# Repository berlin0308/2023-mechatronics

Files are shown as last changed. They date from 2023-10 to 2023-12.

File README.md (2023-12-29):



# I. Introduction

Our robot is designed to be controlled remotely through video streaming. Its primary functions include navigating around and performing vacuuming tasks. Our core philosophy is to minimize space to enhance the robot's agility. In addition, careful study and design of the vacuum is essential to ensure sufficient cleaning efficiency. 
However, fulfilling both requirements simultaneously is not an easy task. In the next chapter, we divided our system design into three main parts: Mechanical Design, Hardware & Electrical Design, and Software & User Interface. 

# II. System Design

## 1.	Mechanical Design

### 1.1 Overview

Our robot is comprised of three layers in a circular design, allowing it to rotate in place. Its diameter is restricted to just 18 centimeters for enhanced agility. The main structural components are in the middle (in x, y axis) and underneath (in z axis) to ensure balance. 

The top layer mainly consists of an Arduino and RPi, forming the core for computation and control. The middle layer houses the vacuum and motor structures, along with the power control circuit. The lowest layer aligns the omnidirectional wheels, drive wheels, and vacuum nozzle at the same height to ensure the vacuum remains close to the ground, maximizing suction efficiency.



For securing each mechanical component, we strictly use keyholes and screws instead of direct adhesion. Additionally, with an emphasis on superior industrial design, the body of the robot features a combination of wood tones and white. This choice underlines a lightweight, minimalist, and homely style. 

### 1.2 Vacuum Design

Unlike other groups using fan-induced duct flow to direct dust into a collection box, we utilized a fan close to the ground to create a pressure difference, sucking in dust. Then, using centrifugal force, it disperses the dust to settle onto the dustbin. 

We adopted this method for two reasons: First, integrating the nozzle and dustbin into a single mechanism reduces space occupation, aligning with our core philosophy. Second, a fan positioned close to the ground minimizes pressure loss.

During the midterm test, we adopted a circular design as shown in Figure (a). However, due to the nozzle being too close to the ground and the opening too narrow, precise alignment was necessary to vacuum up scraps of paper. In the final test version, shown in Figure (b), we precisely adjusted the mechanism's height and enlarged the opening. Additionally, we conceived and validated a fact: a rectangular opening effectively creates turbulence in corners, enhancing the vacuum's cleaning performance.

Figure (c) provides a closer look. The blue region indicates the spatial occupation of the fan. Acting like a pump, the fan generates an airflow (red arrows) that dives into the interior with turbulence induced (orange arrows). The fan then disperses the dust (blue arrows), letting it to settle into the dustbin (grey arrows).



### 1.3 Front Sensor and Robotic Eyes 

During the mid-term test, we employed a video-streaming strategy but encountered visibility issues when the robot was too close to walls. To address this, we installed an ultrasonic sensor at the front for corner detection. Upon detecting a corner, the device activates 'storm' mode, which involves spinning in place with the vacuum on.

In addition, to enhance its appearance and for fun aspects, we equipped the front side with an LCD display that shows different expressions during various states, as illustrated in Figures (a), (b), and (c).



## 2. Hardware & Electrical Design

Figure (a) illustrates our focus on achieving seamless integration of diverse components within a comprehensive circuit to augment both the functionality and power efficiency of the robot. The integrated components encompass a battery box, switch, vacuum motor, wheel motor, motor driver, RGB LED, ultrasonic sensor, camera, LCD, relay, power converter, Raspberry Pi, and Arduino Uno. 

A notable feature of our approach is the incorporation of a power converter in tandem with a relay, facilitating the robot to operate all devices using only a single battery box. This innovation eliminates the necessity for external power sources, setting our design apart from other teams' configurations that commonly rely on supplementary mobile power supplies.



## 3. Software & User Interface

Figure (b) represents the user interface developed by our team for this project. Unlike other groups utilizing App Inventor or other pre-existing toolkits, our team constructed the operational interface using HTML. Beyond the fundamental functionalities of basic directional controls for upward, downward, leftward, and rightward movement, our interface incorporates an additional feature known as the 'storm' function, depicted by the lightning cloud icon in Figure (b). This function enables powerful vacuuming upon reaching areas with accumulated dust.

Furthermore, the background design adopts a cyberpunk style to align with the visually striking appearance of our robotic vacuum cleaner. This cohesive design approach aims to ensure consistency between the device's aesthetics and its user interface.

The innovative use of HTML in crafting the interface sets our project apart, offering a tailored and visually engaging control system for the user. This deliberate design choice not only enhances usability but also complements the futuristic and captivating appeal of our robotic cleaner.

Figure (c) illustrates the conceptual diagram depicting the intercommunication and interaction between backend programs. Through interface buttons, messages are transmitted to 'main.py,' residing within our Raspberry Pi (RPI), which further relays these instructions via serial transmission to the Arduino for execution. This successful process fulfills the objectives of the class, specifically achieving communication and mechanical integration between the RPI and Arduino.
 
All these programs are hosted within our RPI, allowing us to utilize SSH from a computer within the same network domain for remote control. Employing these methods and technologies reflects our aim to simulate real-world operational environments for robotic vacuum cleaners. Typically, these operations involve remote communication via the internet from home environments. Therefore, this concept aligns with the core principle driving the initial design of our software.

# III. Discussion

## 1.	 Challenges

### 1.1	Mechanical Design



### 1.2	Software System Control



## 2.	Test Reviews



# IV.	Appendix

## Members and Teamwork



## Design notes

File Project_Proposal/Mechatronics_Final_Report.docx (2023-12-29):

2023 Fall

Mechatronics and System Design-Mechatronics IV

Final Project Report

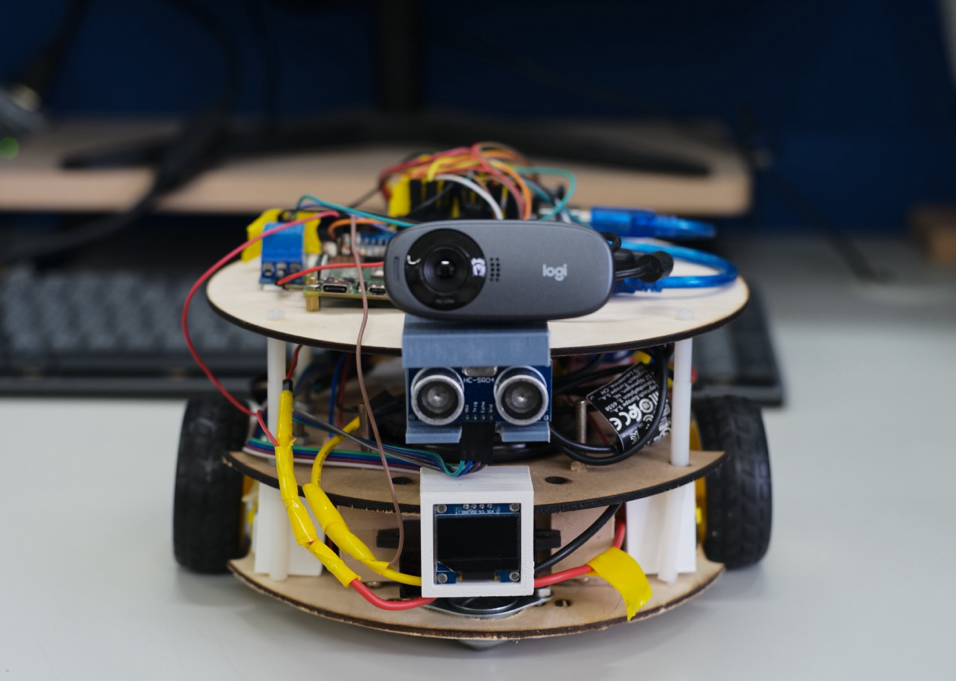
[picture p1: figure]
一張含有 室內, 玩具汽車, 比例模型, 玩具 的圖片 自動產生的描述

Group VI

Members:

B09611007 陳柏霖 (Po-Lin Chen)

B09611010 鄧世群 (Shih-Chun Deng)

B09611043 陳冠霖 (Guan-Lin Chen)

B08204024 陳冠宇 (Kuan-Yu Chen)

Abstract

This project report outlines the design and development of our compact, agile vacuum robot, engineered for remote operation via video streaming. The report delves into three primary areas of system design: Mechanical Design, Hardware & Electrical Design, and Software & User Interface.

In the Mechanical Design section, the report emphasizes the robot’s three-layer circular structure that enables it to rotate in place and maintain balance, with a strictly limited diameter for improved agility. A novel vacuum design with a ground-level fan and centrifugal dust dispersal mechanism is highlighted, showcasing the team’s unique approach to minimizing space while maintaining cleaning efficiency. The design also incorporates ultrasonic sensors and robotic eyes represented by an LCD display for enhanced functionality and interactivity.

Hardware & Electrical Design details the integration of components within the robot’s circuitry to optimize functionality and power efficiency. A key innovation is the use of a single battery box to operate all devices, which effectively reduces excess weight, setting our design apart from other teams that rely on supplementary mobile power supplies.

Software & User Interface development is recognized for its custom HTML-based control interface, featuring a 'storm' function for intensified vacuum cleaning and a cyberpunk-style visual theme to match the robot's aesthetics.

The report also discusses challenges encountered in the system development, with solutions such as adjustments to the robot's height, wheel support, vacuum nozzle shape for the mechanical aspect, and buffering to address with transmitting delays for the software.

Strategic improvements from Mid-term to Final Testing phases, including enhanced practice, corner detection, and 'storm' mode, significantly reduced the time required to complete tasks.

Overall, this project showcases a successful integration of innovative design, component optimization, and user interface development to create a distinctive and efficient robotic vacuum cleaner.

Outline

I. Introduction ……………………………….……….…... 4
II. System Design ………………………………….…….… 4
1. Mechanical Design ………………………………..……….. 4
  1.1 Overview ………………………………………….…….. 4
  1.2 Vacuum Design ……………………………………..… 5
  1.3 Front Sensor and Robotic Eyes ………………… 6
2. Hardware & Electrical Design ………..……………..… 6
3. Software & User Interface …..………………………….. 7
III. Discussion ……………………………………….………. 9
1. Challenges ……………………………………………………… 9
2. Test Reviews …………………………………………..………. 9
IV. Reflections & Suggestions ……………..……….. 10
V. Appendix ………………………………….……………. 11
1. Members and Teamwork ……………………………… 11

I. Introduction

Our robot is designed to be controlled remotely through video streaming. Its primary functions include navigating around and performing vacuuming tasks. Our core philosophy is to minimize space to enhance the robot's agility. In addition, careful study and design of the vacuum is essential to ensure sufficient cleaning efficiency.

However, fulfilling both requirements simultaneously is not an easy task. In the next chapter, we divided our system design into three main parts: Mechanical Design, Hardware & Electrical Design, and Software & User Interface.

II. System Design

1. Mechanical Design

1.1 Overview

Our robot is comprised of three layers in a circular design, allowing it to rotate in place. Its diameter is restricted to just 18 centimeters for enhanced agility. The main structural components are in the middle (in x, y axis) and underneath (in z axis) to ensure balance.

The top layer mainly consists of an Arduino and RPi, forming the core for computation and control. The middle layer houses the vacuum and motor structures, along with the power control circuit. The lowest layer aligns the omnidirectional wheels, drive wheels, and vacuum nozzle at the same height to ensure the vacuum remains close to the ground, maximizing suction efficiency.

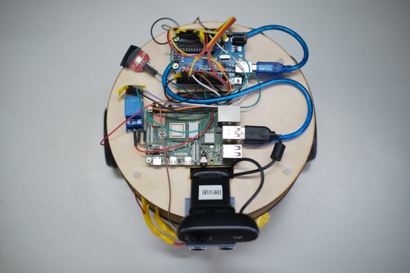
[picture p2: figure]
一張含有 電子工程, 電子產品, 電氣線路, 纜線 的圖片 自動產生的描述
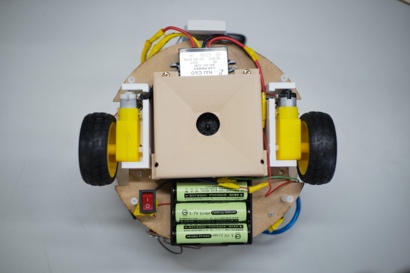
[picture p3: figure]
一張含有 玩具, 汽車零件, 輪胎, 輪 的圖片 自動產生的描述
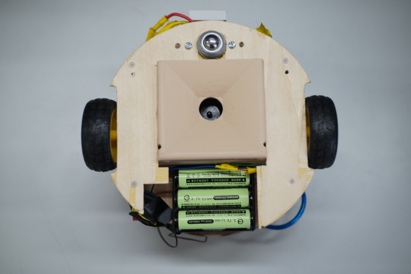
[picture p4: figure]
一張含有 玩具, 汽車零件, 車 的圖片 自動產生的描述

(a) Top layer | (b) Middle layer | (c) Bottom layer

For securing each mechanical component, we strictly use keyholes and screws instead of direct adhesion. Additionally, with an emphasis on superior industrial design, the body of the robot features a combination of wood tones and white. This choice underlines a lightweight, minimalist, and homely style.

1.2 Vacuum Design

Unlike other groups using fan-induced duct flow to direct dust into a collection box, we utilized a fan close to the ground to create a pressure difference, sucking in dust. Then, using centrifugal force, it disperses the dust to settle onto the dustbin.

We adopted this method for two reasons: First, integrating the nozzle and dustbin into a single mechanism reduces space occupation, aligning with our core philosophy. Second, a fan positioned close to the ground minimizes pressure loss.

During the midterm test, we adopted a circular design as shown in Figure (a). However, due to the nozzle being too close to the ground and the opening too narrow, precise alignment was necessary to vacuum up scraps of paper. In the final test version, shown in Figure (b), we precisely adjusted the mechanism's height and enlarged the opening. Additionally, we conceived and validated a fact: a rectangular opening effectively creates turbulence in corners, enhancing the vacuum's cleaning performance.

Figure (c) provides a closer look. The blue region indicates the spatial occupation of the fan. Acting like a pump, the fan generates an airflow (red arrows) that dives into the interior with turbulence induced (orange arrows). The fan then disperses the dust (blue arrows), letting it to settle into the dustbin (grey arrows).

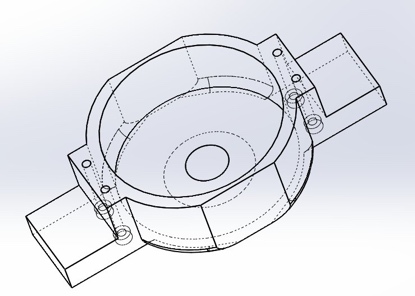
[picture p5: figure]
一張含有 寫生, 圖畫, 圓形, 圖表 的圖片 自動產生的描述
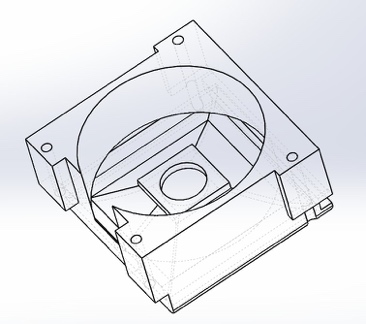
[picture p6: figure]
一張含有 寫生, 圖畫, 線條藝術, 圖表 的圖片 自動產生的描述
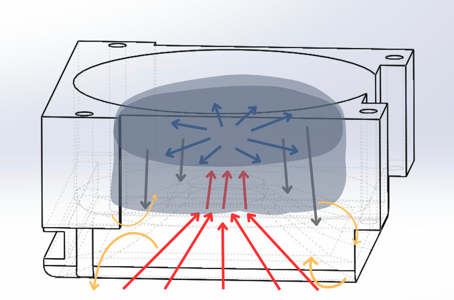
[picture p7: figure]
一張含有 行, 寫生, 設計, 藝術 的圖片 自動產生的描述

(a) Mid-term Version | (b) Final Version | (c) Fluid Velocity Field

1.3 Front Sensor and Robotic Eyes

During the mid-term test, we employed a video-streaming strategy but encountered visibility issues when the robot was too close to walls. To address this, we installed an ultrasonic sensor at the front for corner detection. Upon detecting a corner, the device activates 'storm' mode, which involves spinning in place with the vacuum on. (https://drive.google.com/file/d/1HJC3LFM9daGVQigIeRPdedcw-CsZ7EiV/view?usp=sharing)

In addition, to enhance its appearance and for fun aspects, we equipped the front side with an LCD display that shows different expressions during various states, as illustrated in Figures (a), (b), and (c).

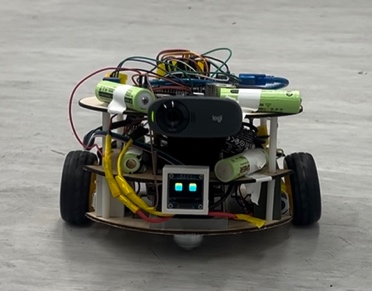
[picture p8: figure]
一張含有 輪, 輪胎, 動力運動, 汽車零件 的圖片 自動產生的描述
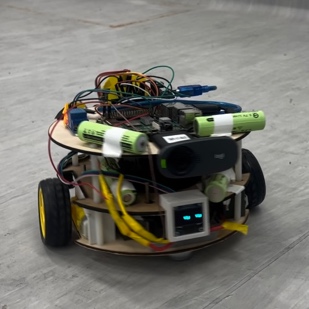
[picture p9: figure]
一張含有 輪, 輪胎, 車輛, 動力運動 的圖片 自動產生的描述
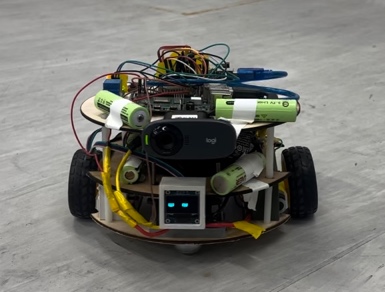
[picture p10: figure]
一張含有 輪, 輪胎, 汽車零件, 動力運動 的圖片 自動產生的描述

(a) Moving Forward | (b) Turning Left | (c) Turning Right

2. Hardware & Electrical Design

Figure (a) illustrates our focus on achieving seamless integration of diverse components within a comprehensive circuit to augment both the functionality and power efficiency of the robot. The integrated components encompass a battery box, switch, vacuum motor, wheel motor, motor driver, RGB LED, ultrasonic sensor, camera, LCD, relay, power converter, Raspberry Pi, and Arduino Uno.

A notable feature of our approach is the incorporation of a power converter in tandem with a relay, facilitating the robot to operate all devices using only a single battery box. This innovation eliminates the necessity for external power sources, setting our design apart from other teams' configurations that commonly rely on supplementary mobile power supplies.

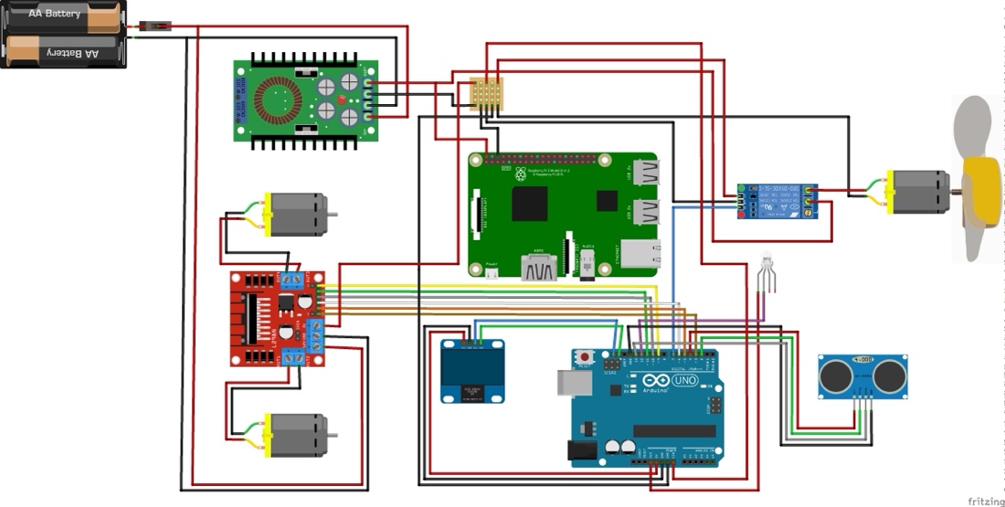
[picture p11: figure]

(a)

3. Software & User Interface

Figure (b) represents the user interface developed by our team for this project. Unlike other groups utilizing App Inventor or other pre-existing toolkits, our team constructed the operational interface using HTML. Beyond the fundamental functionalities of basic directional controls for upward, downward, leftward, and rightward movement, our interface incorporates an additional feature known as the 'storm' function, depicted by the lightning cloud icon in Figure (b). This function enables powerful vacuuming upon reaching areas with accumulated dust.

Furthermore, the background design adopts a cyberpunk style to align with the visually striking appearance of our robotic vacuum cleaner. This cohesive design approach aims to ensure consistency between the device's aesthetics and its user interface.

The innovative use of HTML in crafting the interface sets our project apart, offering a tailored and visually engaging control system for the user. This deliberate design choice not only enhances usability but also complements the futuristic and captivating appeal of our robotic cleaner.

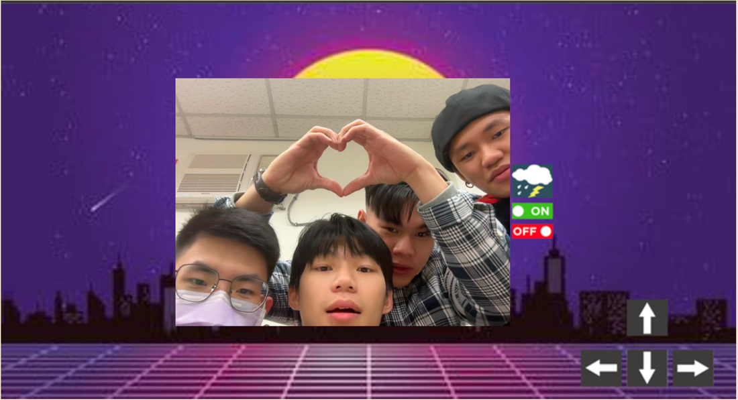
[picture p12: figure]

(b)

Figure (c) illustrates the conceptual diagram depicting the intercommunication and interaction between backend programs. Through interface buttons, messages are transmitted to 'main.py,' residing within our Raspberry Pi (RPI), which further relays these instructions via serial transmission to the Arduino for execution. This successful process fulfills the objectives of the class, specifically achieving communication and mechanical integration between the RPI and Arduino.

All these programs are hosted within our RPI, allowing us to utilize SSH from a computer within the same network domain for remote control. Employing these methods and technologies reflects our aim to simulate real-world operational environments for robotic vacuum cleaners. Typically, these operations involve remote communication via the internet from home environments. Therefore, this concept aligns with the core principle driving the initial design of our software.

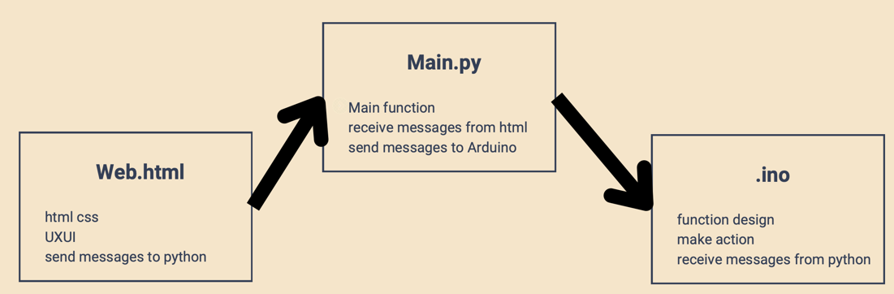
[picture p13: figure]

(c)

III. Discussion

1. Challenges
  1.1 Mechanical Design

Problems | Solutions
- Our vacuum was designed to be placed under the body of the vehicle, close to the ground. - The wheels often become splayed outward after running for a while, which caused our vehicle to get stuck during the journey. | - Adjusted vehicle’s height by adding a layer. - Made precise adjustments of the omni-wheel. - Redesigned the shape of the vacuum nozzle. - Designed and installed a bracket for motors.

  1.2 Software System Control

Problems | Solutions
- Delay when using UI buttons during the Mid-term Test, leading to multiple presses. - Excessive turning angles for left and right movements, making it difficult to accurately reach the targets. | - Introduced a buffer in the main program to alleviate the delay issue. - Adjusted control parameters for forward, backward, left, and right movements.

2. Test Reviews

Midterm Test | Final
- Insufficient testing before the mid-term. - Couldn't view the floor, preventing us from determining whether we had aligned with the target. - Wasted time wandering. | - Conducted more practice sessions for both manual and video-streaming control. - Introduced corner detection and ‘storm’ mode to efficiently complete the task. - Saved over half of the time during the final test.

VI. Reflections & Suggestions
1. B09611007陳柏霖 (Po-Lin Chen)

關於這堂課，我覺得專題有吸塵的元素蠻有趣的，也可以讓大家發揮創意。不過專題花費的時間其實超過想像，我主要負責的是機構設計，原以為期中之後車體定型就有時間協助軟體開發自走功能，沒想到期中之後車體要加裝一層、3D列印的支架和鎖孔都要更新、吸塵口機構迭代五次，其實也不夠時間做自走車了，剩下的時間只好拿來做角落偵測和機器人眼睛。認真算下來這學期花了68小時課外時間，以3學分的課而言有點多但還可接受。給課程的建議是可以更重視報告的呈現和工業設計，兩者都是系上其他課程未要求卻極為重要的素養，作為Capstone課程若能加強培養必能使同學畢業後更加體面且專業。

2. B09611010 鄧世群 (Shih-Chun Deng)

我負責電路設計與實踐的部分，包含線路焊接、硬體系統整合和改善。期中花費許多時間在與設計硬體的組員討論機構和線路的配合，因為我們想要盡可能將整組系統做得更加緊湊，節省空間和重量。組員都是四年級，大家每週的行程都相當不同，因此一開始明確的任務分配變得非常重要。使我們能夠根據任務內容配合出席的組員，更加有效率的完成任務。我認為這堂課的設計還需幾次的嘗試才能夠建立出完整的測試規則，避免太多變因造成不公平的可能。但還是非常感謝教授與助教的用心，大家都在這堂課學習到許多。

3. B09611043 陳冠霖 (Guan-Lin Chen)

我主要負責的部分是RPI主程式以及協助部分機構設計以及操作者，期中前我們把軟硬體的連線都大致完成，原本期待期末能以自走的方式呈現，結果期中發現吸塵有些狀況，加上對規則計分不夠熟悉，表現不佳。因此期末我們決定捲土重來，把機構重新修改，改善軟體以及熟練操作，期末有明顯進步。這學期的過程中很感謝組員的互相合作，加上不斷地修改調整以及溝通，讓我們從0開始到最後有一定的成果。也很感謝老師跟助教在這學期的協助，協助我們有一個能展現的舞台，作為大學4年最後一堂必修課，是一個很難忘的回憶。

4. B08204024 陳冠宇 (Kuan-Yu Chen)

在這個團隊中，我的主要責任是軟體架構，包括UX/UI設計和不同平台框架 間的溝通。大部分工作其實在期中評估之前就完成了，但由於期中成績不 盡理想，我們後來對程式進行了一些修改，以在專題結束時更加順暢地運 行。我認為這門課作為我們學業的最後一站，主題和內容都非常貼合。在 這個過程中需要的技能都是我們四年學習的累積，和這些同學一起完成最 後的專題任務感覺格外特別。看著大家從一開始的困惑到能夠高效地完成 分派的任務，這種轉變讓人深受觸動。唯一的遺憾是期中時間稍微不足 （雖然在期末有改善），以及某些規則可能使得比賽某些方面不太公平。 但無論如何，我非常感激大家的奉獻，也感謝我們的教授和助教所提供的 指導。

VII. Appendix
1. Members and Teamwork

| Po-Lin Chen | Shih-Chun Deng | Kuan-Yu Chen | Gaun-Lin Chen
Project Proposal | Mechanical Design, Materials, Proofreading, Refinement | System Diagram, Electrical Design | User Interface | Difficulties
~ Mid-term | components design, manufacturing, assembly | circuits, power, hardware testing | frontend, user interface | backend
Mid-term Trial & Test | testing | testing | testing, robot operator | testing
~ Final | components iterations, corner detect, robotic eyes | power circuits update | software fine-tuning | component design
Final Trial & Test | fine-tuning | fine-tuning | fine-tuning | fine-tuning, robot operator
Final Presentation | Mechanical Design, slides proofreading | Electrical Design, presenter | Software & UI, presenter | Discussion
Final Report | Abstract, Introduction, Mechanical Design, Proofreading, Refinement | Hardware & Electrical Design | Software & User Interface | Discussion

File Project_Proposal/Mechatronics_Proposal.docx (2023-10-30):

2023 Fall

Mechatronics and System Design-Mechatronics IV

Final Project Proposal

Group VI:

Members:

B09611007 陳柏霖 (Po-Lin Chen)

B09611010 鄧世群 (Shih-Chun Deng)

B09611043 陳冠霖 (Kaun-Lin Chen)

B08204024 陳冠宇 (Kuan-Yu Chen)

Outline

I. System Design
1. System Diagram
2. Mechanical Design
3. Electrical Design
4. User Interface
II. Materials
1. Material List
2. Manufactural Methods
III. Project Plans
1. Gantt Chart
2. Roles and Responsibilities
IV. Difficulties

I. System Design

1. System Diagram

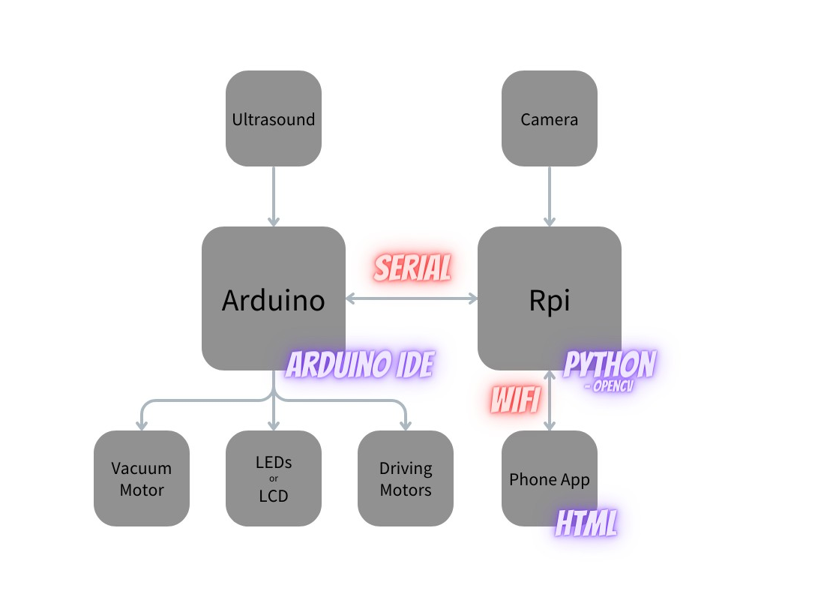
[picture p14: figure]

2. Mechanical Design

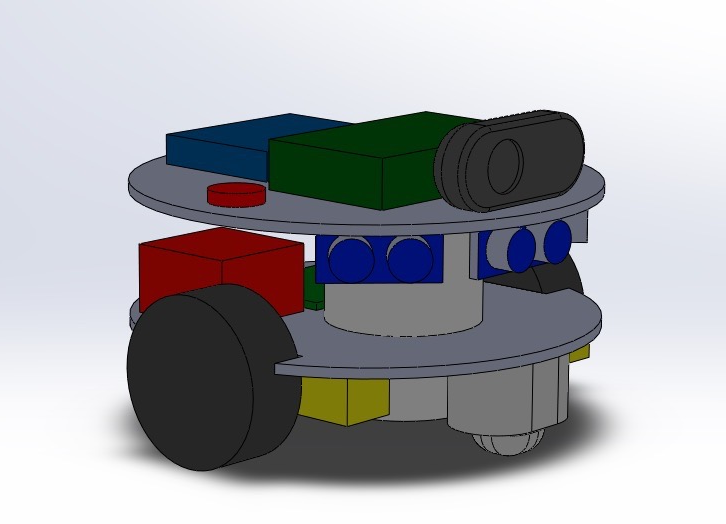
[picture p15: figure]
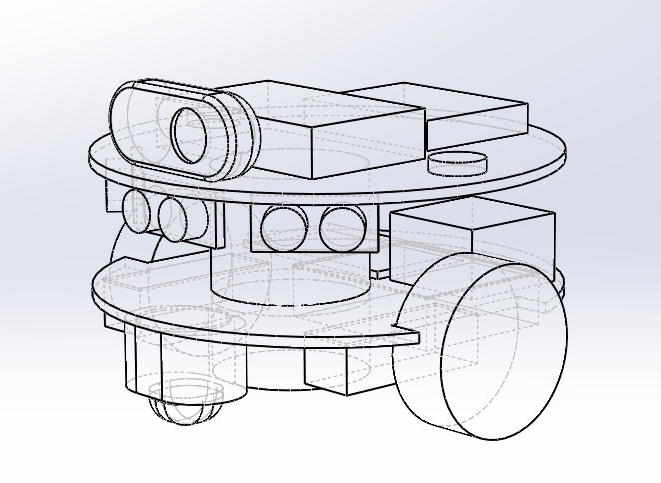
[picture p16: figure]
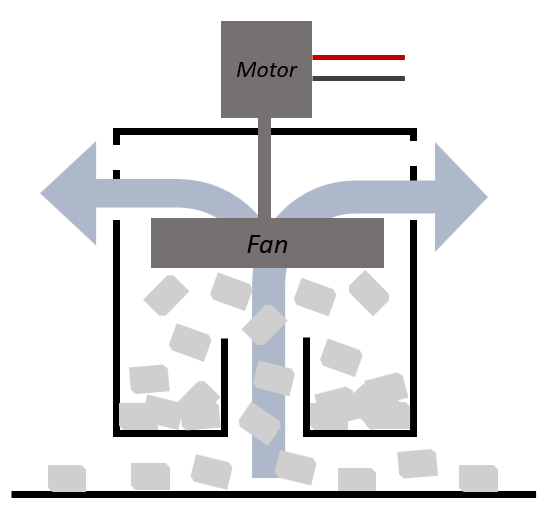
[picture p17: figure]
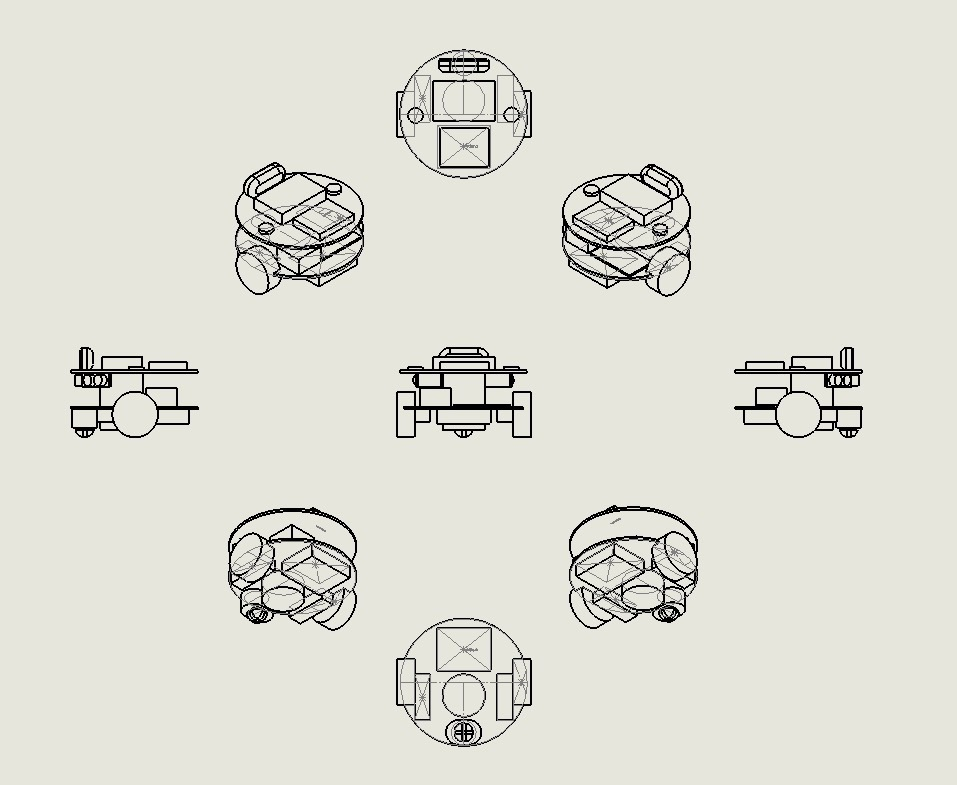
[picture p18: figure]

3. Electrical Design

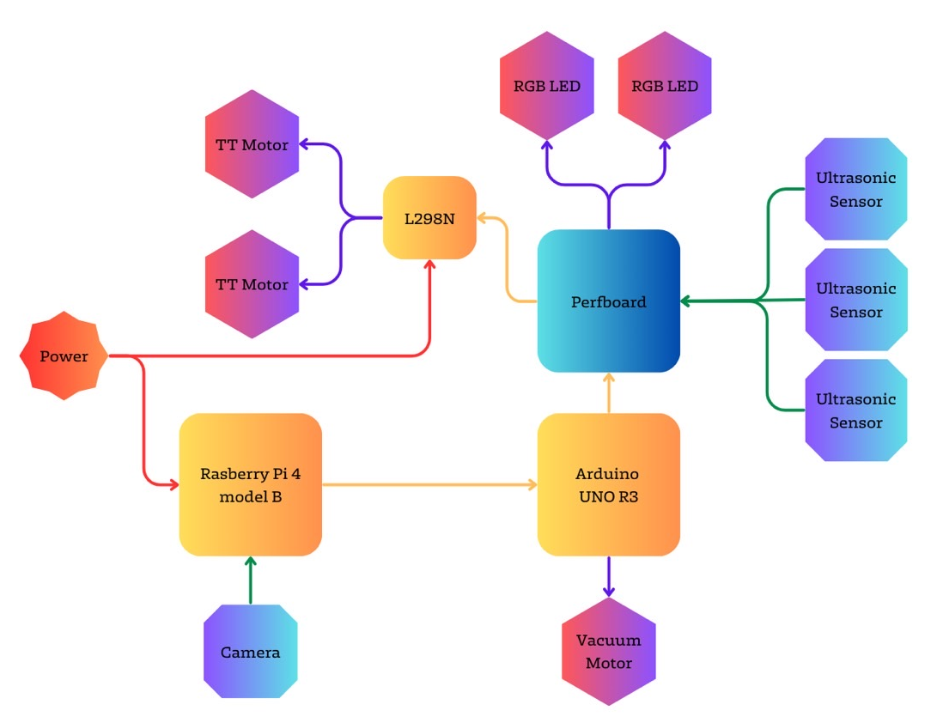
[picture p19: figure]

4. User Interface

II. Materials

1. Material List

ID | Part | Source
1 | Raspberry Pi 4 model B | BB Lab
2 | Arduino UNO R3 | BB Lab
3 | Arduino cable | Mechatronics IV
4 | VGA-HDMI cable | Mechatronics IV
5 | DC motor | Mechatronics IV
6 | TT motor*2 | Mechatronics IV
7 | Wheel | Mechatronics IV
8 | Ultrasonic sensor*3 | Mechatronics IV, BB Lab
9 | L298N | Mechatronics IV
10 | Bread Board | Mechatronics IV
11 | Perfboard | BB Lab
12 | MicroSD card | Mechatronics IV
13 | Logitech webcam | Mechatronics IV
14 | 18650 Lithium battery*3 | Mechatronics IV
15 | Battery case | Mechatronics IV
16 | RGB LED | BB Lab

*Additional parts to be purchased: None

2. Manufacturing Methods

ID | Component | Method
A | Undercarriage | Laser cutting
B | Upper Layer | Laser cutting
C | Camera Mount | 3D printing
D | Ultrasonic Sensor Mount | 3D printing
E | Omni-wheel Connector | 3D printing
F | Vacuum Bracket | 3D printing
G | Rpi, Arduino, Perfboard, L298N, TT Motor, RGB LED, Battery Fixtures | Keyholes and Standoffs

III. Project Plans

1. Gantt Chart

| 9/ 22 | 9/ 29 | 10/ 6 | 10/ 13 | 10/ 20 | 10/ 27 | 11/ 3 | 11/ 10 | 11/ 17 | 11/ 24 | 12/ 1 | 12/ 8 | 12/ 15 | 12/ 22
Mech | Mechanical Design | | Assembly & Testing | | | | | New Feature Implementation | | | | Fine- Tuning
SW | UI Design | | Frontend / Backend Development | | | System Integration
HW | Unit Testing | | Hardware Integration
Pres | Project Proposal | | | | | | | | | | | Final Presentation

2. Roles and Responsibilities

Work Assignment | Responsible Individual
Mechanical Design | Po-Lin
Manufacturing & Assembly | Po-Lin, Kaun-Lin
Hardware Development | Shih-Chun
Hardware Integration | Shih-Chun, Kaun-Lin
User Interface Design | Kuan-Yu
Software Development | Kuan-Yu
System Integration | Po-Lin, Shih-Chun, Kaun-Lin, Kuan-Yu
Final Presentation | Shih-Chun, Kuan-Yu

IV. Difficulties

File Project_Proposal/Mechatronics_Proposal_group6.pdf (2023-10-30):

### 2023 Fall

### Mechatronics and System Design-Mechatronics IV

# Final Project Proposal

### Group VI: ChDennnng Design®

### Members:

### B09611007 陳柏霖 (Po-Lin Chen)

### B09611010 鄧世群 (Shih-Chun Deng)

### B09611043 陳冠霖 (Guan-Lin Chen)

### B08204024 陳冠宇 (Kuan-Yu Chen)

# Outline

## I. System Design

### 1. System Diagram

### 2. Mechanical Design

### 3. Electrical Design

### 4. User Interface

## II. Materials

### 1. Material List

### 2. Manufactural Methods

## III. Project Plans

### 1. Gantt Chart

### 2. Roles and Responsibilities

## IV. Difficulties

# I. System Design

## 1. System Diagram

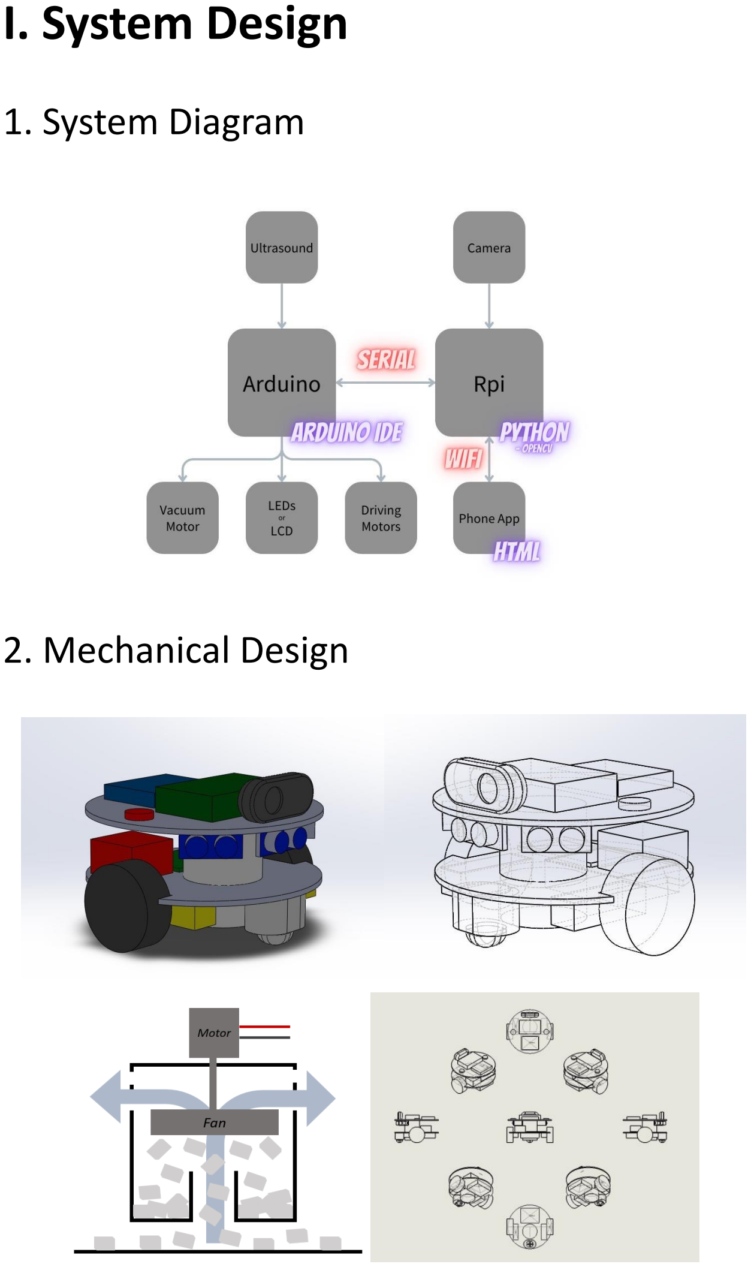
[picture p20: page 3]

## 2. Mechanical Design

## 3. Electrical Design

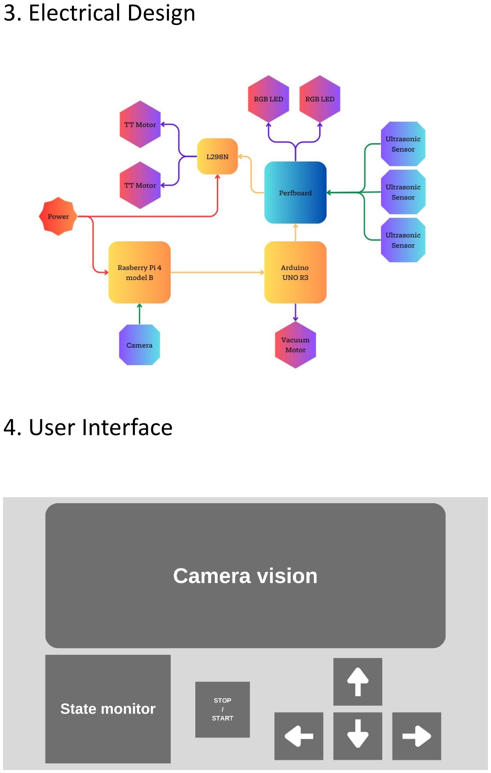
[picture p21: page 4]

## 4. User Interface

# II. Materials

## 1. Material List

ID | Part | Source
1 | Raspberry Pi 4 model B | BB Lab
2 | Arduino UNO R3 | BB Lab
3 | Arduino cable | Mechatronics IV
4 | VGA-HDMI cable | Mechatronics IV
5 | DC motor | Mechatronics IV
6 | TT motor*2 | Mechatronics IV
7 | Wheel | Mechatronics IV
8 | Ultrasonic sensor*3 | Mechatronics IV, BB Lab
9 | L298N | Mechatronics IV
10 | Bread Board | Mechatronics IV
11 | Perfboard | BB Lab
12 | MicroSD card | Mechatronics IV
13 | Logitech webcam | Mechatronics IV
14 | 18650 Lithium battery*3 | Mechatronics IV
15 | Battery case | Mechatronics IV
16 | RGB LED | BB Lab

*Additional parts to be purchased: None

## 2. Manufacturing Methods

ID | Component | Method
A | Undercarriage | Laser cutting
B | Upper Layer | Laser cutting
C | Camera Mount | 3D printing
D | Ultrasonic Sensor Mount | 3D printing
E | Omni-wheel Connector | 3D printing
F | Vacuum Bracket | 3D printing
G | Rpi, Arduino, Perfboard, L298N, TT Motor, RGB LED, Battery Fixtures | Keyholes and Standoffs

# III. Project Plans

## 1. Gantt Chart

| 9/ 22 | 9/ 29 | 10/ 6 | 10/ 13 | 10/ 20 | 10/ 27 | 11/ 3 | 11/ 10 | 11/ 17 | 11/ 24 | 12/ 1 | 12/ 8 | 12/ 15 | 12/ 22
Mech | Mechanical Design | | Assembly & Testing | | | | | New Feature Implementation | | | | Fine-Tuning
SW | UI Design | | Frontend / Backend Development | | | System Integration
HW | Unit Testing | | Hardware Integration
Pres | Project Proposal | | | | | | | | | | | Final Presentation

## 2. Roles and Responsibilities

Work Assignment | Responsible Individual
Mechanical Design | Po-Lin
Manufacturing & Assembly | Po-Lin, Guan-Lin
Hardware Development | Shih-Chun
Hardware Integration | Shih-Chun, Guan-Lin
User Interface Design | Kuan-Yu
Software Development | Kuan-Yu
System Integration | Po-Lin, Shih-Chun, Guan-Lin, Kuan-Yu
Final Presentation | Shih-Chun, Kuan-Yu

# IV. Difficulties

⚫ | How to prevent paper from falling out before the motor is turned off.
| Create a curved structure in the vacuum cleaner hose similar to a drainage pipe, ensuring sufficient duration of suction and a strong suction force.
⚫ | Both the camera and ultrasonic sensor are located in the front, and it may take some time to adjust their angles for sensing.
| Both are placed in the front for the sake of front-to-rear weight balance, and the vehicle's circular body design is intended to minimize friction during rotation.

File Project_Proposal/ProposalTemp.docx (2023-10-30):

# 機電整合與系統設計-機電整合(四)

# 期末專題計畫書

組別：

組員: 學號姓名

1. 機械設計概念與設計圖
  1. 風扇設計
  2. 吸塵口設計
  3. 邊刷設計
  4. 各個零件配置與重量、變位計算
2. 電路系統設計概念與方塊圖
  1. 整體架構圖
  2. 預計使用到的軟體
  3. 遠端控制預計流程圖
3. 材料
  1. 列舉會用到的材料和電子零件
  2. 是否會使用到3D列印機？
  3. 是否有需要新購買其他零件？
4. 期程規劃（甘特圖）與分工表

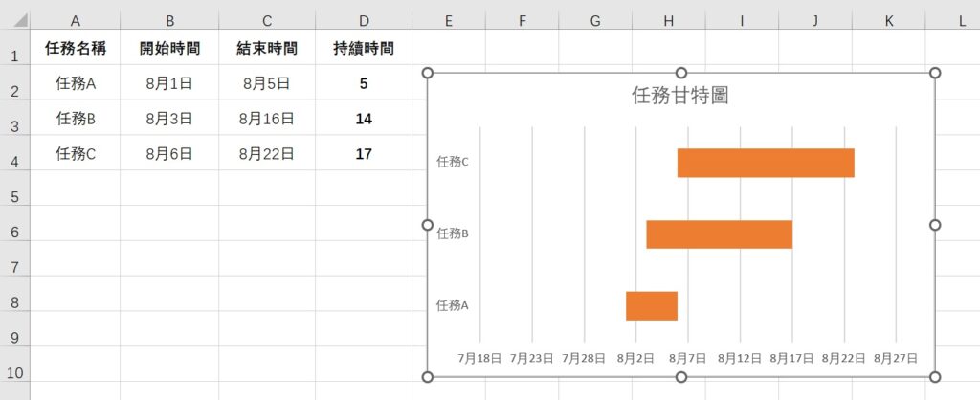
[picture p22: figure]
在Excel中創建甘特圖 步驟7

5. 預想關卡突破可能會遇到的問題

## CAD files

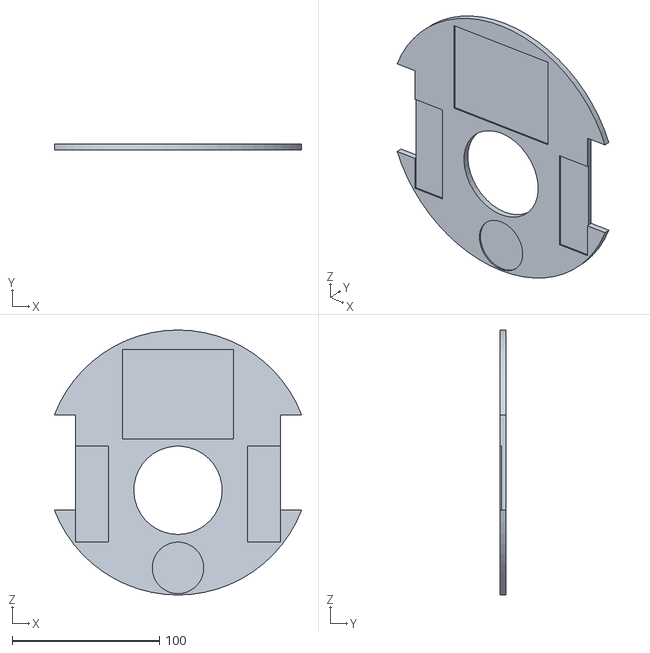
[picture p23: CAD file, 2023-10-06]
3D_components/STL/Assembly_STL - Layers-1.STL
168.0 x 4.00 x 180.0

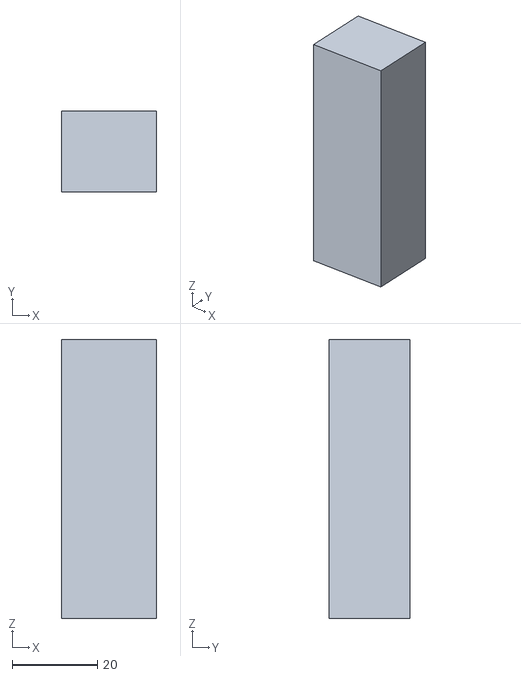
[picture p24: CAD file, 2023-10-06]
3D_components/STL/Assembly_STL - wheel_motor-2.STL
22.4 x 19.0 x 65.5

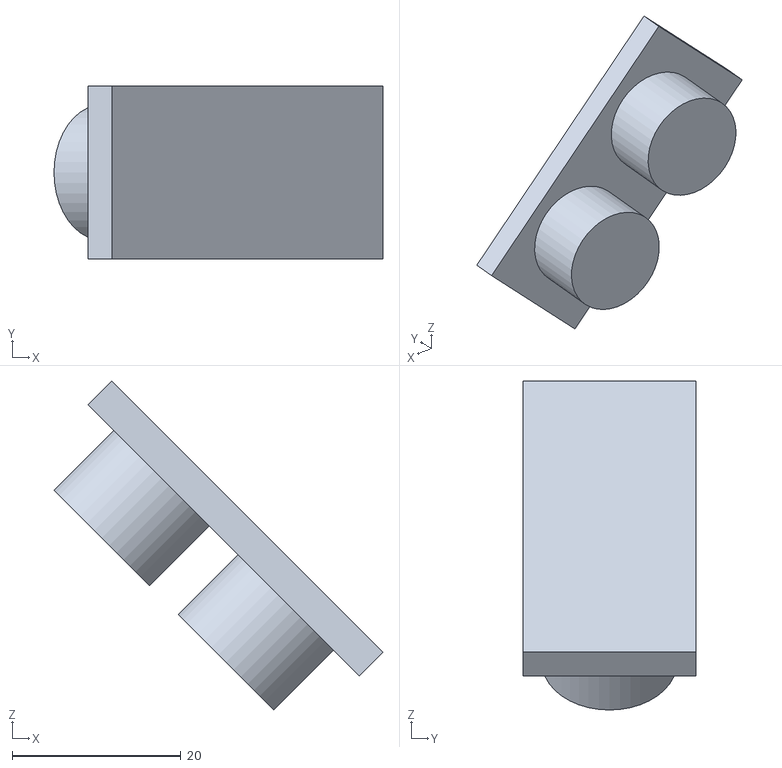
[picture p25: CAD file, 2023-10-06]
3D_components/STL/Assembly_STL - Ultrasonic-3.STL
39.0 x 20.5 x 39.0

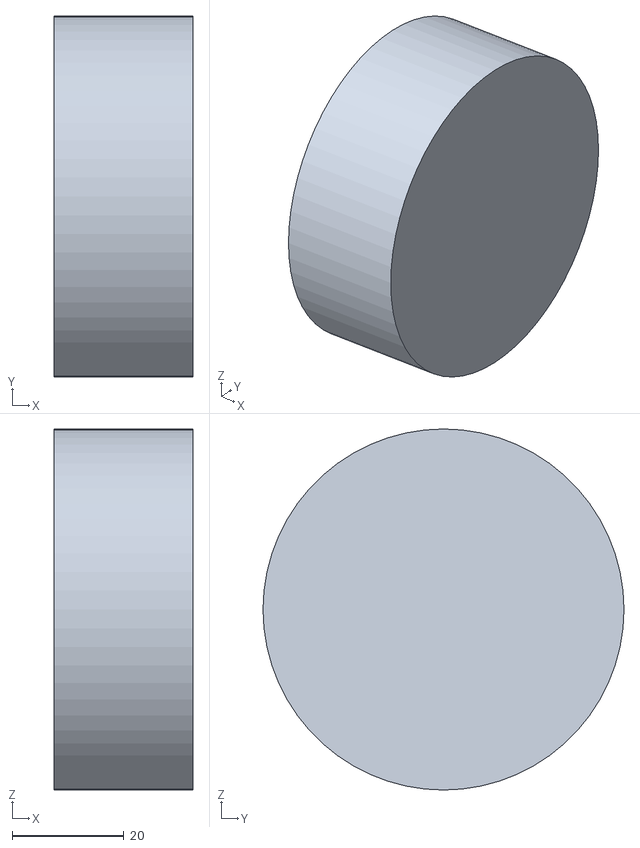
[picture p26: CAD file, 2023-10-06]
3D_components/STL/Assembly_STL - wheel-3.STL
24.8 x 64.5 x 64.5

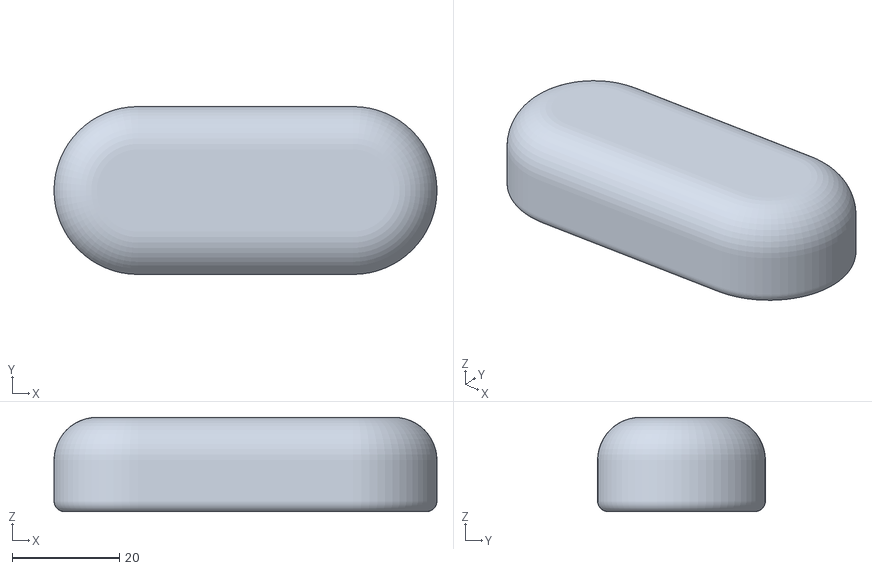
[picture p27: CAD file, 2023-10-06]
3D_components/STL/Assembly_STL - webcam-1.STL
71.4 x 31.3 x 17.6

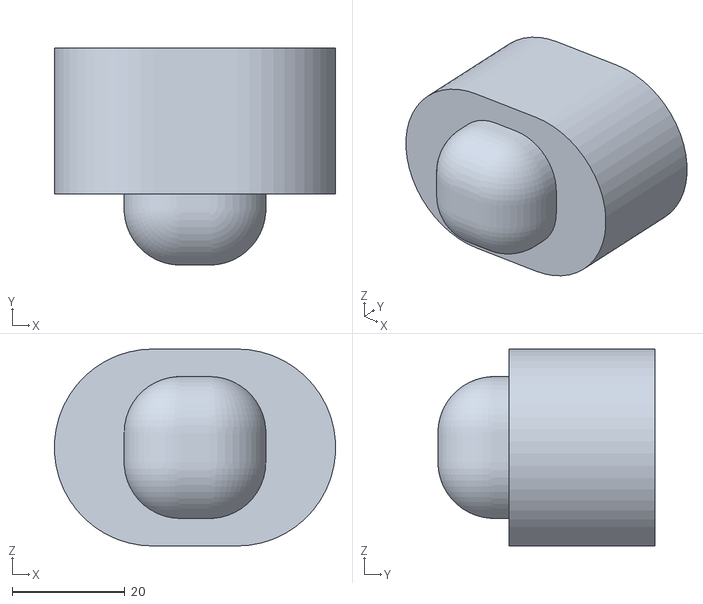
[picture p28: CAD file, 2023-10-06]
3D_components/STL/Assembly_STL - omni_wheel-1.STL
49.9 x 38.6 x 35.0

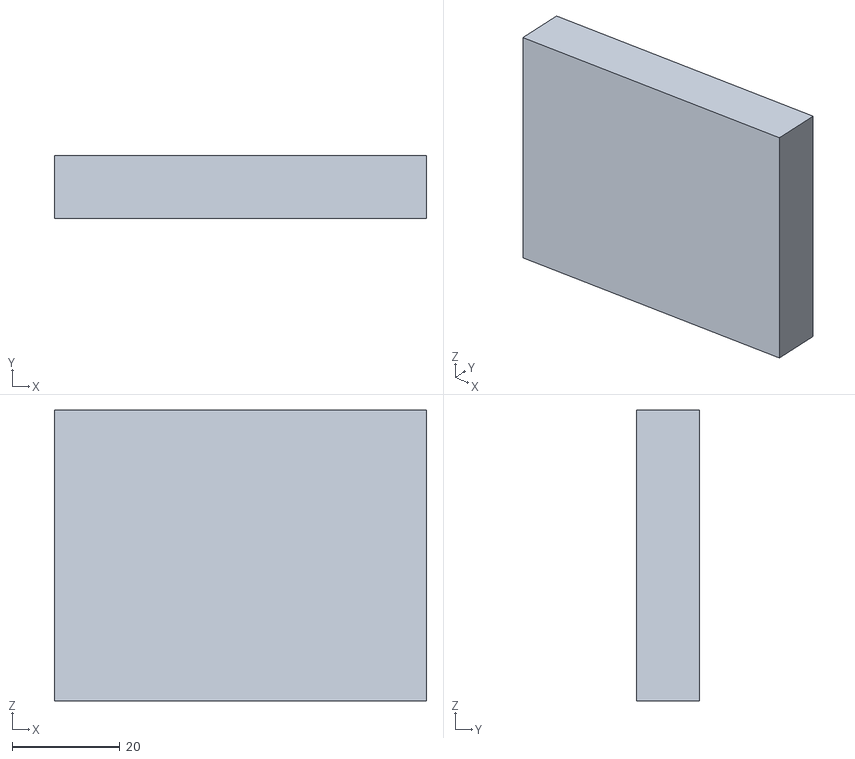
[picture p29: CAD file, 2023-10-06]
3D_components/STL/Assembly_STL - Arduino_UNO-1.STL
69.0 x 11.6 x 53.9

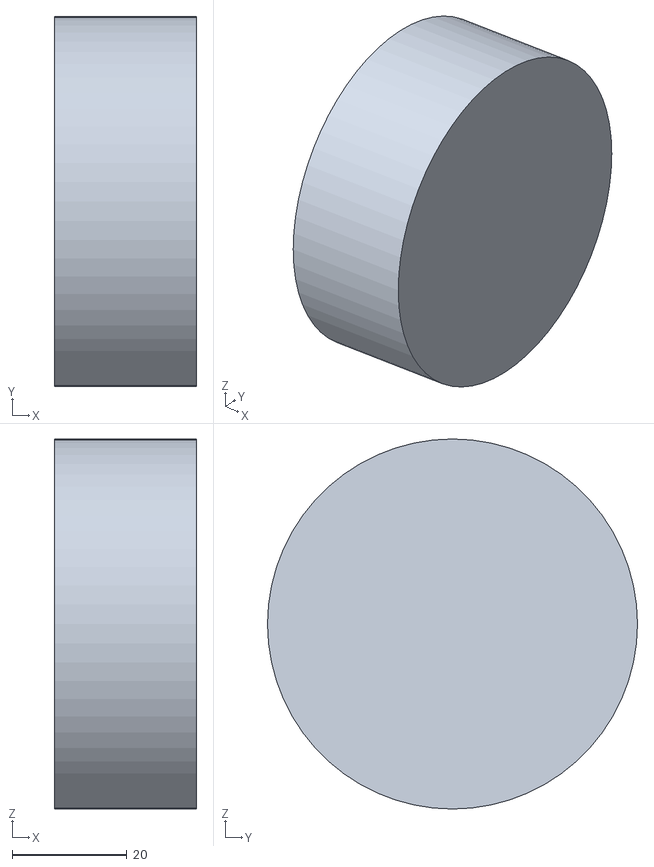
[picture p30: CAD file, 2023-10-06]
3D_components/STL/Assembly_STL - wheel-2.STL
24.8 x 64.5 x 64.5

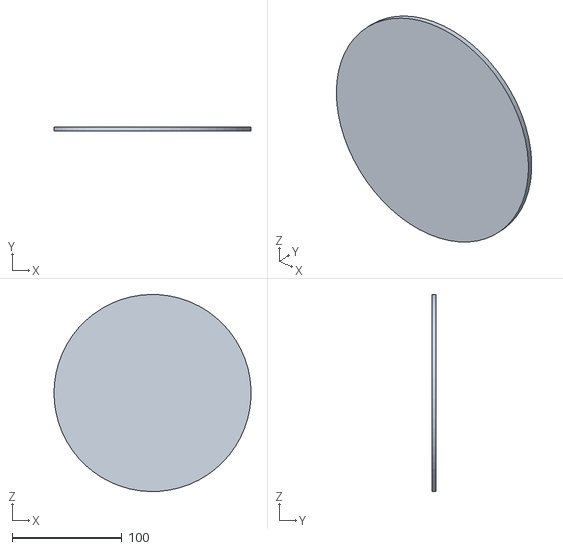
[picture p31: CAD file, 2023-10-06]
3D_components/STL/Assembly_STL - layer_upper-1.STL
179.9 x 4.00 x 179.9

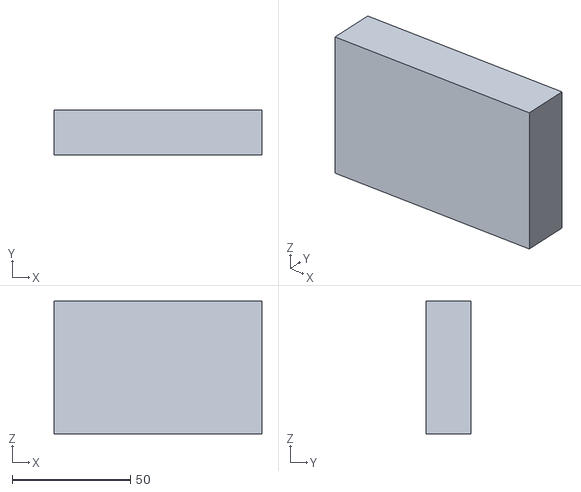
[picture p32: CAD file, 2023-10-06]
3D_components/STL/Assembly_STL - Raspberry_Pi_4-1.STL
88.1 x 19.0 x 56.2

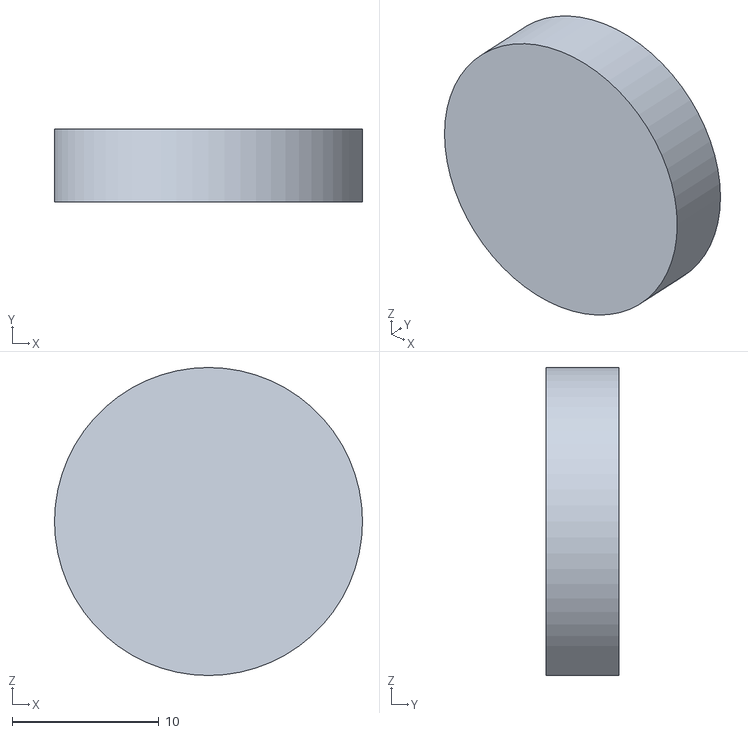
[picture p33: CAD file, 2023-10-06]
3D_components/STL/Assembly_STL - rgb_LED-1.STL
21.0 x 5.00 x 21.0

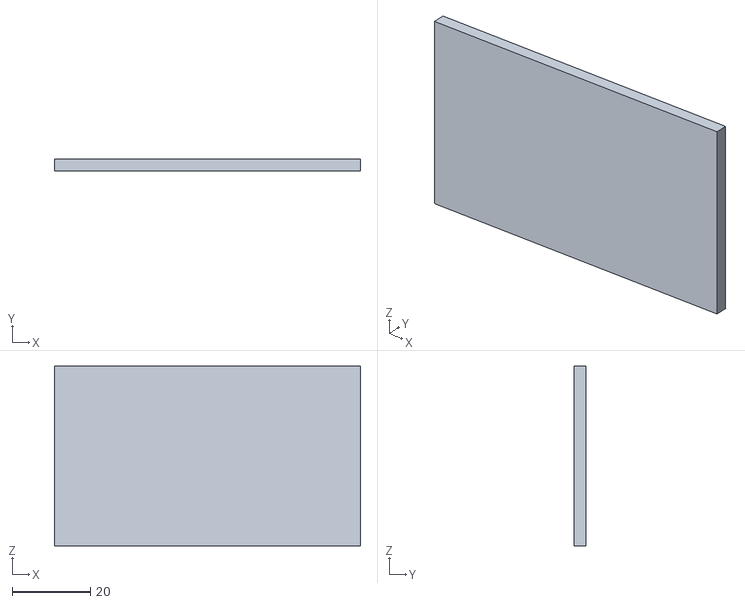
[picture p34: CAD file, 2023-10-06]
3D_components/STL/Assembly_STL - perforated_board-1.STL
78.4 x 3.00 x 46.0

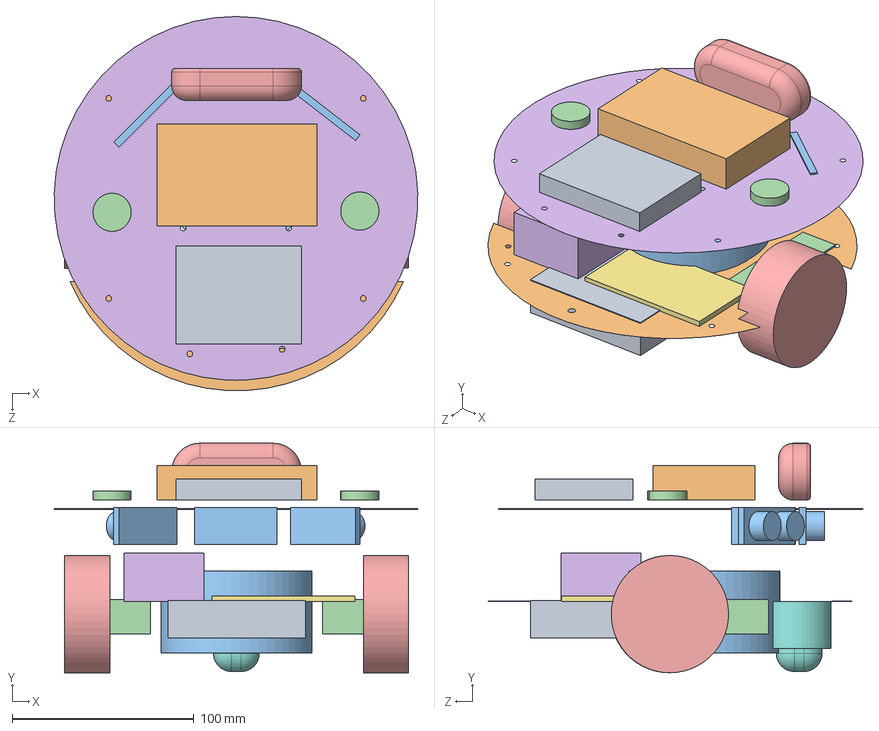
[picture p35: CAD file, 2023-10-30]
3D_components/Assembly.SLDASM
199.9 x 126.2 x 205.6 mm
battery
Layer_lower
vacuum
wheel_motor x 2
wheel x 2
L298N
perforated_board
omni_wheel
Arduino_UNO
Raspberry_Pi_4
Ultrasonic x 3
rgb_LED x 2
webcam
Layers_Upper

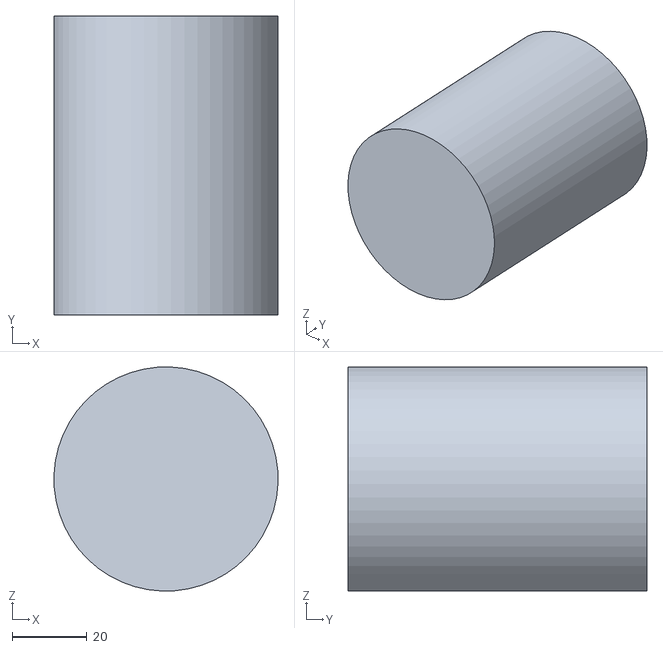
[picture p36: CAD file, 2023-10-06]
3D_components/STL/Assembly_STL - vacuum-1.STL
59.9 x 80.0 x 59.9

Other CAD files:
3D_components/STL/Assembly_STL - wheel_motor-1.STL
3D_components/STL/Assembly_STL - Ultrasonic-1.STL
3D_components/STL/Assembly_STL - rgb_LED-2.STL
3D_components/STL/Assembly_STL - battery-1.STL
3D_Components_V2/Oled_mount.SLDPRT
3D_Components_V2/Oled_mount.STL
3D_Components_V2/Undercarriage.SLDPRT
3D_Components_V2/Undercarriage_New.DXF
3D_Components_V2/Undercarriage_New.SLDPRT
3D_Components_V2/motor_support.SLDPRT
3D_Components_V2/motor_support.STL
3D_Components_V2/motor_support_R.STL
3D_Components_V2/motor_support_V2.STL
3D_Components_V2/motor_support_v3.STL
3D_Components_V2/vacuum_entry.SLDPRT
3D_Components_V2/vacuum_entry.STL
3D_Components_V2/vacuum_entry_V2.STL
3D_Components_V2/vacuum_entry_v3.STL
3D_Components_V2/vacuum_entry_v4.STL
3D_Components_V2/vacuum_entry_v5.STL
3D_components/Arduino_UNO.SLDPRT
3D_components/Assembly_projection.SLDDRW
3D_components/DXF/Layer_Lower.DXF
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

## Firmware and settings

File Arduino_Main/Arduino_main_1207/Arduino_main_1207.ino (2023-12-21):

#include <Wire.h>
#include <Adafruit_GFX.h>
#include <Adafruit_SSD1306.h>

#define SCREEN_WIDTH 128
#define SCREEN_HEIGHT 64
#define OLED_RESET -1
Adafruit_SSD1306 display(SCREEN_WIDTH, SCREEN_HEIGHT, &Wire, OLED_RESET);

#include "eyes.h"
void forward(int Ftime, bool closeStop=true, bool slowMode=false);
void backward(int Btime, bool slowMode=false);

int vac = 7;

// Motor A connections
int enA = 3;
int in1 = 6;
int in2 = 5;
// Motor B connections
int enB = 9;
int in3 = 11;
int in4 = 10;               

int redLED = 12;

int const ultra5V = 4;
int const trigPin = 2;
int const echoPin = 13;
int Duration;
int Distance;

void setup() {
  Serial.begin(9600);
   
  pinMode(ultra5V, OUTPUT);
  digitalWrite(ultra5V, HIGH);
  pinMode(trigPin, OUTPUT);
  pinMode(echoPin, INPUT);
  digitalWrite(trigPin, LOW);

  pinMode(redLED, OUTPUT);
  digitalWrite(redLED, HIGH);


  pinMode(vac, OUTPUT);
  // pinMode(vac, INPUT);
  
  vacoff();

  // vacon();
  

	// Set all the motor control pins to outputs
	pinMode(enA, OUTPUT);
	pinMode(enB, OUTPUT);
	pinMode(in1, OUTPUT);
	pinMode(in2, OUTPUT);
	pinMode(in3, OUTPUT);
	pinMode(in4, OUTPUT);
	
	// Turn off motors - Initial state
	digitalWrite(in1, LOW);
	digitalWrite(in2, LOW);
	digitalWrite(in3, LOW);
	digitalWrite(in4, LOW);

  if (!display.begin(SSD1306_SWITCHCAPVCC, 0x3c)) {
    Serial.println(F("SSD1306 allocation failed"));
    for (;;);
  }

  display.display();
  display.clearDisplay();

}

void loop() {

  stop();
  display.clearDisplay();
  display.drawBitmap(16, 8, eye0, 32, 32, WHITE);
  display.drawBitmap(80, 8, eye0, 32, 32, WHITE);
  display.display();
  // vacoff();

  if (Serial.available() > 0) {
    char command = Serial.read();
  

    switch (command) {
      case 'A':
        digitalWrite(redLED, LOW);
        display.clearDisplay();
        display.drawBitmap(16, 8, eye13i, 32, 32, WHITE);
        display.drawBitmap(80, 8, eye13d, 32, 32, WHITE);
        display.display();
        delay(2000);
      
        digitalWrite(redLED, HIGH);
        display.clearDisplay();
        display.drawBitmap(16, 8, eye13d, 32, 32, WHITE);
        display.drawBitmap(80, 8, eye13i, 32, 32, WHITE);
        display.display();
        delay(300);
        break;
      case 'F':
        display.clearDisplay();
        display.drawBitmap(16, 8, eye1, 32, 32, WHITE);
        display.drawBitmap(80, 8, eye1, 32, 32, WHITE);
        display.display();
        forward(500, true);
        break;
      case 'B':
        display.clearDisplay();
        display.drawBitmap(16, 8, eye2, 32, 32, WHITE);
        display.drawBitmap(80, 8, eye2, 32, 32, WHITE);
        display.display();
        backward(300);
        break;
      case 'L':
        display.clearDisplay();
        display.drawBitmap(36, 8, eye9, 32, 32, WHITE);
        display.drawBitmap(100, 8, eye9, 32, 32, WHITE);
        display.display();
        left(65); // 65
        break;
      case 'R':
        display.clearDisplay();
        display.drawBitmap(-4, 8, eye9, 32, 32, WHITE);
        display.drawBitmap(60, 8, eye9, 32, 32, WHITE);
        display.display();
        right(65);
        break;
      case 'S':
        display.clearDisplay();
        display.drawBitmap(16, 8, eye8, 32, 32, WHITE);
        display.drawBitmap(80, 8, eye8, 32, 32, WHITE);
        display.display();
        stop();
        break; 
      case 'V':
        display.clearDisplay();
        display.drawBitmap(16, 8, eye8, 32, 32, WHITE);
        display.drawBitmap(80, 8, eye8, 32, 32, WHITE);
        display.display();
        vacon();
        break;
      case 'N':
        vacoff();
        break;
      case 'T':
        digitalWrite(vac, HIGH);
        whirl(5700);
        digitalWrite(vac, LOW);
        // storm();
        display.clearDisplay();
        display.drawBitmap(16, 8, eye1, 32, 32, WHITE);
        display.drawBitmap(80, 8, eye1, 32, 32, WHITE);
        display.display();
        break;
    }
    Serial.flush();
  }

}

void forward(int Ftime, bool closeStop=true, bool slowMode=false) {

  if(!slowMode){
    analogWrite(enA, 220);
    analogWrite(enB, 160);
  }else{
    analogWrite(enA, 150);
    analogWrite(enB, 120);
  }

	digitalWrite(in1, HIGH);
	digitalWrite(in2, LOW);
	digitalWrite(in4, LOW);
	digitalWrite(in3, HIGH);

  if(closeStop){
    for(int i=0;i<10;i++){
      assertDistance();
      delay(Ftime/10);
    }
  }

}


void backward(int Btime, bool slowMode=false) {

  if(!slowMode){
    analogWrite(enA, 200);
    analogWrite(enB, 120);
  }else{
    analogWrite(enA, 150);
    analogWrite(enB, 120);
  }

	digitalWrite(in1, LOW);
	digitalWrite(in2, HIGH);
	digitalWrite(in4, HIGH);
	digitalWrite(in3, LOW);

  delay(Btime);
}

void left(int Ltime) {
  
  analogWrite(enA, 200);
	analogWrite(enB, 120);

	digitalWrite(in1, LOW);
	digitalWrite(in2, HIGH);
	digitalWrite(in4, LOW);
	digitalWrite(in3, HIGH);

  delay(Ltime);
}

void right(int Rtime) {

  analogWrite(enA, 200);
	analogWrite(enB, 120);

	digitalWrite(in1, HIGH);
	digitalWrite(in2, LOW);
	digitalWrite(in4, HIGH);
	digitalWrite(in3, LOW);

  delay(Rtime);
}

void stop() {
  digitalWrite(in1, LOW);
	digitalWrite(in2, LOW);
	digitalWrite(in4, LOW);
	digitalWrite(in3, LOW);
  
}

void vacon() {

	digitalWrite(vac, HIGH);

  delay(100);

}

void vacoff() {

	digitalWrite(vac, LOW);

}

void assertDistance(){
  digitalWrite(trigPin, HIGH);
  delay(10);
  digitalWrite(trigPin, LOW);
  Duration = pulseIn(echoPin, HIGH);
  Distance = Duration * 0.034 / 2; // unit: cm
  // Serial.println(Distance);
  if(Distance<22){
    stop();
  }
}

void adjustDistance(int d){
  while(true){
    digitalWrite(trigPin, HIGH);
    delay(10);
    digitalWrite(trigPin, LOW);
    Duration = pulseIn(echoPin, HIGH);
    Distance = Duration * 0.034 / 2; // unit: cm
    if((Distance-d)<3 && (Distance-d)>-3){
      stop();
      break;
    }
    if((Distance-d)>3){
      forward(200, false, true);
    }
    if((Distance-d)<-3){
      backward(200, true);
    }
  }
}

void storm(){


  adjustDistance(18);
  delay(1000);

  right(270);
  stop();
  delay(1000);

  adjustDistance(18);
  delay(1000);

  left(250);
  stop();
  delay(1000);
  
  digitalWrite(vac, HIGH);
  
  whirl(5700);

  digitalWrite(vac, LOW);
}

void whirl(int Wtime) {

  analogWrite(enA, 200);
	analogWrite(enB, 80);

	digitalWrite(in1, HIGH);
	digitalWrite(in2, LOW);
	digitalWrite(in4, HIGH);
	digitalWrite(in3, LOW);

  delay(Wtime);
}

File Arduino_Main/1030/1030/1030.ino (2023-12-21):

int ledPin1 = 13; // 第一個LED接腳
int ledPin2 = 4; // 第二個LED接腳

// int const trigPin = 13;
// int const echoPin = 12;
// int Duration;
// int Distance;

int vac = 7;

// Motor A connections
int enA = 3;
int in1 = 5;
int in2 = 6;
// Motor B connections
int enB = 9;
int in3 = 10;
int in4 = 11;

void setup() {
  Serial.begin(9600);
  pinMode(ledPin1, OUTPUT); // 設定LED接腳為輸出
  pinMode(ledPin2, OUTPUT); // 設定LED接腳為輸出

  // pinMode(trigPin, OUTPUT);
  // pinMode(echoPin, INPUT);
  // digitalWrite(trigPin, LOW);

  pinMode(vac, OUTPUT);
  digitalWrite(vac, HIGH);

	// Set all the motor control pins to outputs
	pinMode(enA, OUTPUT);
	pinMode(enB, OUTPUT);
	pinMode(in1, OUTPUT);
	pinMode(in2, OUTPUT);
	pinMode(in3, OUTPUT);
	pinMode(in4, OUTPUT);
	
	// Turn off motors - Initial state
	digitalWrite(in1, LOW);
	digitalWrite(in2, LOW);
	digitalWrite(in3, LOW);
	digitalWrite(in4, LOW);

}

void loop() {
  // digitalWrite(trigPin, HIGH); // 發射超音波
  // delay(10);
  // digitalWrite(trigPin, LOW);
  // Duration = pulseIn(echoPin, HIGH); // 超音波發射到接收的時間
  // Distance = Duration * 0.034 / 2; // 計算距離(cm)
  // Serial.println(Distance);s
  stop();
  vacoff();

  if (Serial.available() > 0) {
    char command = Serial.read();
  

    switch (command) {
      case '1':
        digitalWrite(ledPin1, HIGH); // 打開第一個LED
        break;
      case '2':
        digitalWrite(ledPin1, LOW); // 關閉第一個LED
        break;
      case '3':
        digitalWrite(ledPin2, HIGH); // 打開第二個LED
        break;
      case '4':
        digitalWrite(ledPin2, LOW); // 關閉第二個LED
        break;
      case 'F':
        forward(); // 向前运动
        break;
      case 'B':
        backward(); // 向后运动
        break;
      case 'L':
        left(); // 向左运动
        break;
      case 'R':
        right(); // 向右运动
        break;
      case 'S':
        stop(); // 停止运动
        break;
      case 'V':
        vacon();
        break;
      case 'N':
        vacoff(); // 停止运动
        break;
      case 'T':
        digitalWrite(vac, LOW);
        forward();
        delay(300);
        right();
        delay(300);
        break;
    }
    Serial.flush();
  }

}

void forward(void) {

  analogWrite(enA, 125);
	analogWrite(enB, 125);

	digitalWrite(in1, HIGH);
	digitalWrite(in2, LOW);
	digitalWrite(in3, HIGH);
	digitalWrite(in4, LOW);

  delay(100);

}

void backward(void) {

  analogWrite(enA, 125);
	analogWrite(enB, 125);

	digitalWrite(in1, LOW);
	digitalWrite(in2, HIGH);
	digitalWrite(in3, LOW);
	digitalWrite(in4, HIGH);

  delay(100);
}

void left(void) {
  
  analogWrite(enA, 125);
	analogWrite(enB, 125);

	digitalWrite(in1, HIGH);
	digitalWrite(in2, LOW);
	digitalWrite(in3, LOW);
	digitalWrite(in4, HIGH);

  delay(100);
}

void right(void) {

  analogWrite(enA, 125);
	analogWrite(enB, 125);

	digitalWrite(in1, LOW);
	digitalWrite(in2, HIGH);
	digitalWrite(in3, HIGH);
	digitalWrite(in4, LOW);

  delay(100);
}

void stop() {
  digitalWrite(in1, LOW);
	digitalWrite(in2, LOW);
	digitalWrite(in3, LOW);
	digitalWrite(in4, LOW);
  
}

void vacon() {

	digitalWrite(vac, LOW);

  delay(100);

}

void vacoff() {

	digitalWrite(vac, HIGH);

}

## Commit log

2023-10-30 arduino 1007
    [18650 battery single enclosure.STEP, 18650 battery single enclosure.X_T, Arduino_UNO.SLDPRT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]
2023-12-21 final update
    [18650 battery single enclosure.STEP, 18650 battery single enclosure.X_T, Layer_lower.SLDPRT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]
